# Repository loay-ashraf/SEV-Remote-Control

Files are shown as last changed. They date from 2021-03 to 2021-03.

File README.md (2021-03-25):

# SEV Remote Control
Smart Electric Vehicle remote control implemented using AVR 8-bit microcontroller and Android companion app as a part of EV car conversion graduation project for Mechatronics Engineering Bachelor - Fall 2018.

## Overview
This section gives an overview of the system.

### Concept

SEV remote control is done via means of bluetooth communication between AVR controller board and any bluetooth-enabled device (Android smartphone for example).

### System Layout
System is divided into two separate modules that communicate with each other to acheive the desired output, which are:

#### SEV Controller Board Module

Controller board controls a set of relays and DAC units each connected to a specific actuator in the car.

#### SEV Companion App Module

Companion app sends commands via bluetooth to control each actuator.

## Discussion
This section discusses desicions made regarding design and implementation.

### Microcontroller

We opted for ATmega32 for SEV controller board as it has USART module and enough pins to control relays and DACs.

### Communication Protocol

We used USART protocol in order to communicate with the HC-05 bluetooth module.

### Android IDE

We used free MIT App Inventor as we lacked experience in Android app development while App Inventor offered shallow learning curve and a ton of tutorials available.

## Screenshots

[Screenshots of the companion app](Software/Companion%20App/Screenshots)

## Built With
- Atmel Studio 7 - The official AVR IDE
- AVR-gcc V5.4 - C compiler
- GNU Make - auto-generated makefile
- MIT App Inventor - Android IDE
- CadSoft EAGLE - PCB design tool

## Authors
Loay Ashraf - <loay.ashraf.96@gmail.com>

Mohamed Gamal - <muhammed.gamal051@gmail.com>

## License
This project is licensed under the MIT License - see the LICENSE.md file for details

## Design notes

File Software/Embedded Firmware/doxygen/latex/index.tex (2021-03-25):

\begin{DoxyAuthor}{Author}
Loay Ashraf \href{mailto:loay.ashraf.96@gmail.com}{\tt loay.\+ashraf.\+96@gmail.\+com} 
\end{DoxyAuthor}
\begin{DoxyVersion}{Version}
1.\+0.\+0
\end{DoxyVersion}
This program is implemented on A\+Tmega16/32 running at 16 M\+HZ C\+PU clock, it basically receives commands from Android companion application via Bluetooth using the widely common H\+C-\/05 Bluetooth Module, it acts upon the command received by -\/for example-\/ turning ON a relay which activates certain feature of the vehicle; means of feedback include battery voltage and speed of the motor.

\begin{DoxySeeAlso}{See also}
\mbox{\hyperlink{main_8c}{main.\+c}} 
\end{DoxySeeAlso}

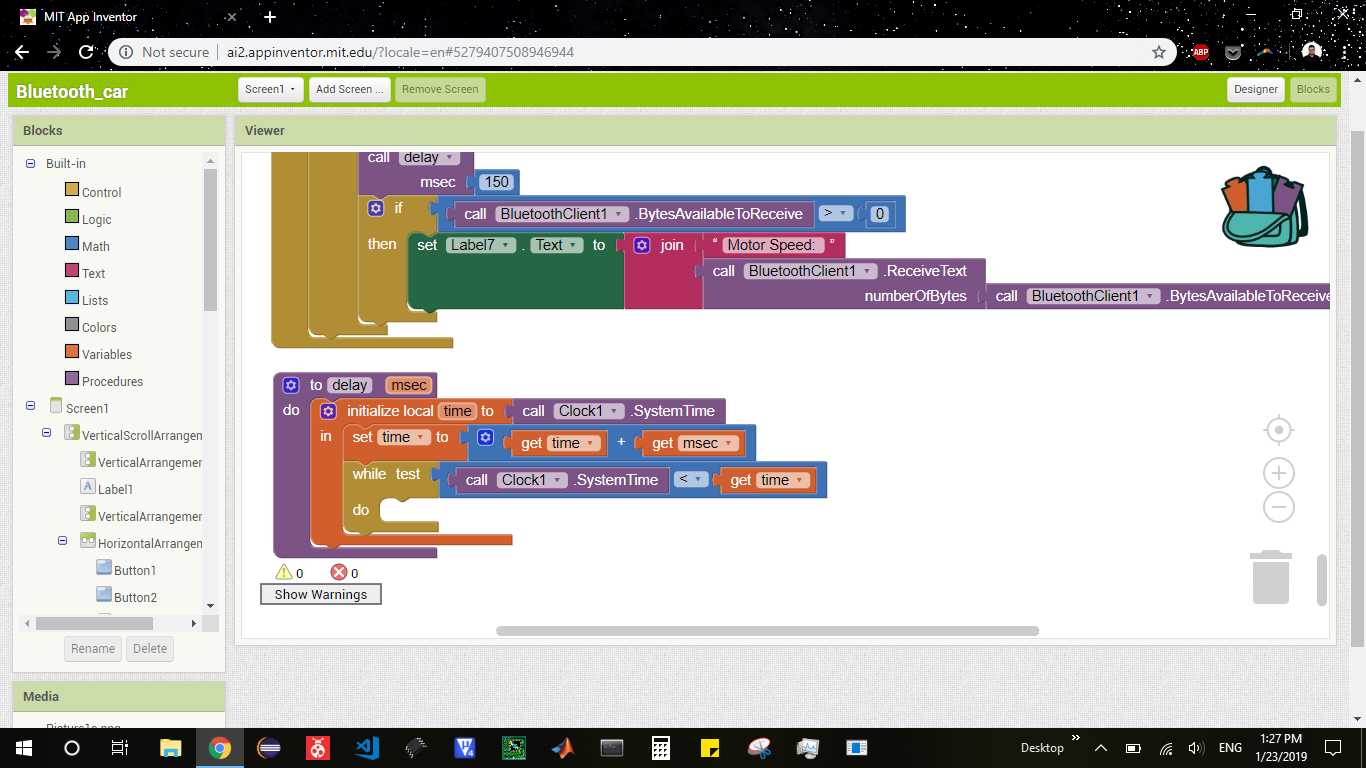
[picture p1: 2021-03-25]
Software/Companion App/Screenshots/App inventor/Screenshot (27).png

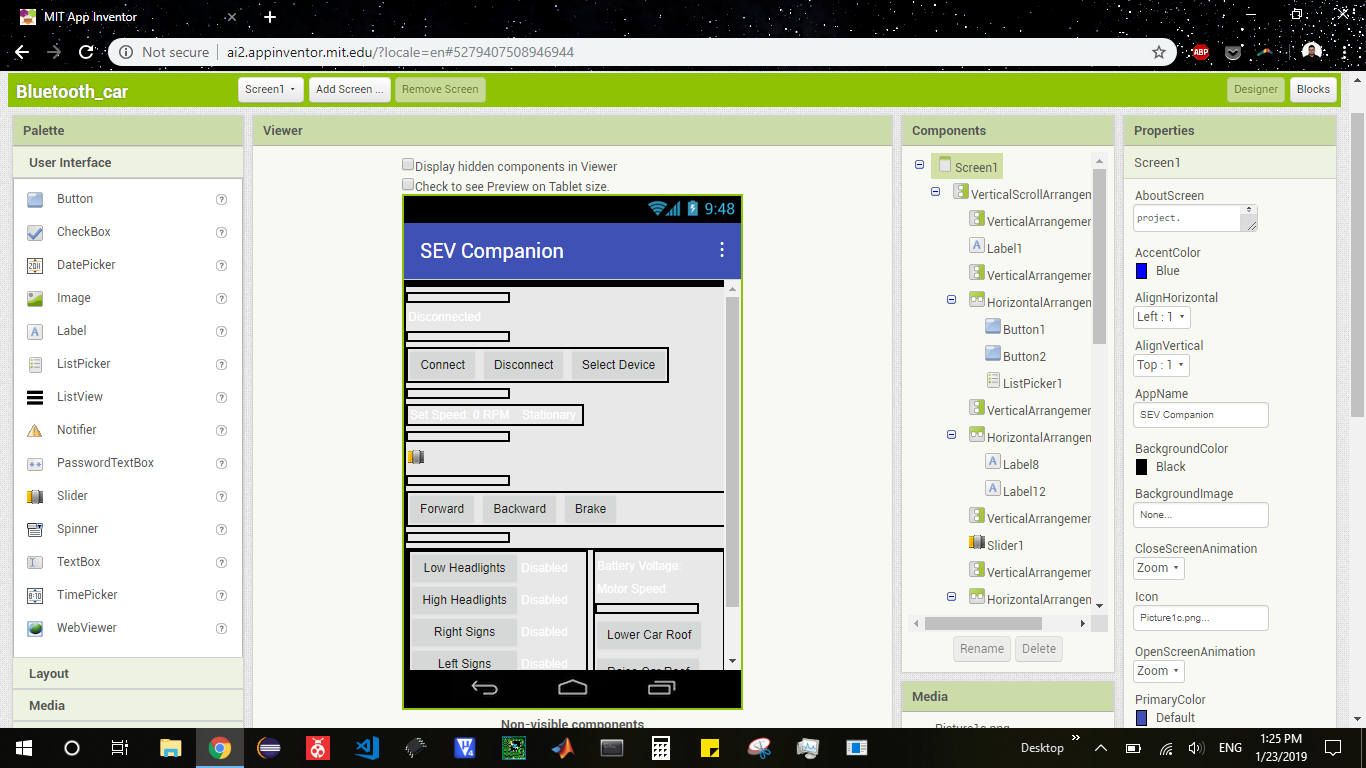
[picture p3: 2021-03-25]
Software/Companion App/Screenshots/App inventor/Screenshot (18).png

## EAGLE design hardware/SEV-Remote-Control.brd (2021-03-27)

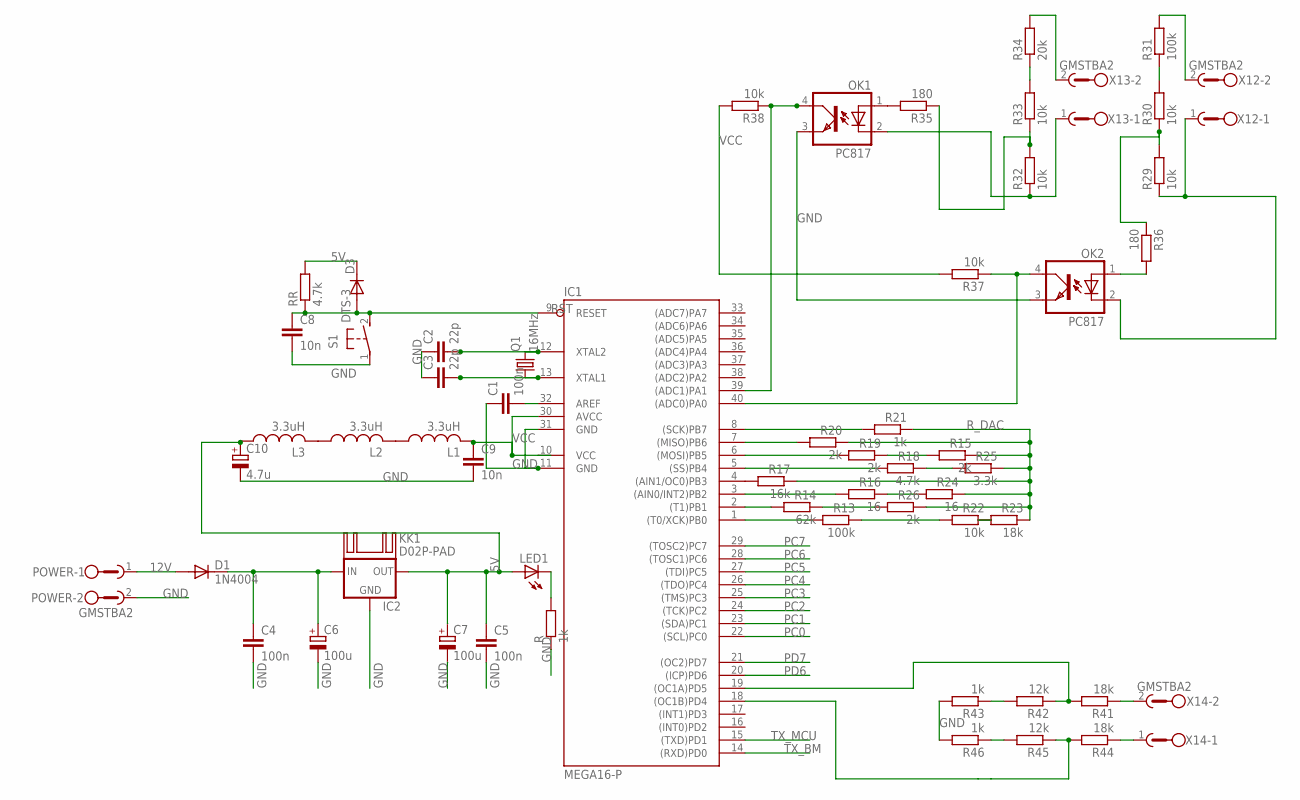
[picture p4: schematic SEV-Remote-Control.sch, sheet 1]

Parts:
C1, C4, C5: 100n; C025-025X050
C2, C3: 22p; C025-025X050
C6, C7: 100u; E2,5-6
C8, C9: 10n; C025-025X050
C10: 4.7u; E2,5-6
D1: 1N4004; DO41-10
D3: 1N4148DO35-10; DO35-10
IC1: MEGA16-P; DIL40
IC2: 78XXS
KK1: D02P-PAD; D02PA-PAD
L1, L2, L3: 3.3uH; 0207/7
LED1: LED5MM
OK1, OK2: PC817; DIL04
POWER: GMSTBA2
Q1: 16MHz; HC49/S
R, R21, R43, R46: 1k; 0207/10
R13, R31: 100k; 0207/10
R14: 62k; 0207/10
R15, R19, R20, R26: 2k; 0207/10
R16, R24: 16; 0207/10
R17: 16k; 0207/10
R18: 4.7k; 0207/10
R22, R29, R30, R32, R33, R37, R38: 10k; 0207/10
R23, R41, R44: 18k; 0207/10
R25: 3.3k; 0207/10
R34: 20k; 0207/10
R35, R36: 180; 0207/10
R42, R45: 12k; 0207/10
RR: 4.7k; 0207/10
S1: DTS-3
X12, X13, X14: GMSTBA2

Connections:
5V: C5.1, C7.+, C10.+, D3.C, IC2.OUT, L3.1, LED1.A, RR.2
12V: D1.A, POWER.1; also elsewhere on the board
GND: C1.1, C2.1, C3.1, C4.2, C5.2, C6.-, C7.-, C8.2, C9.2, C10.-, IC1.11 (GND), IC1.31 (GND), IC2.GND, OK1.3 (EMIT), OK2.3 (EMIT), POWER.2, R.1, R43.2, R46.2, S1.1; also elsewhere on the board
IN: C4.1, C6.+, D1.C, IC2.IN
unnamed: R15.2, R19.1
unnamed: R13.1, R22.2
unnamed: LED1.K (C), R.2
unnamed: C2.2, IC1.12 (XTAL2), Q1.2
unnamed: R22.1, R23.2
unnamed: C1.2, IC1.32 (AREF)
unnamed: R16.1, R24.2
unnamed: C3.2, IC1.13 (XTAL1), Q1.1
unnamed: R18.1, R25.2
unnamed: R14.1, R26.2
unnamed: L1.1, L2.2
unnamed: L2.1, L3.2
unnamed: R29.2, R30.1, R36.1
unnamed: R30.2, R31.1
unnamed: R31.2, X12.2
unnamed: IC1.40 ((ADC0)PA0), OK2.4 (COL), R37.1
unnamed: OK1.1 (A), R35.2
unnamed: R33.2, R34.1
unnamed: R34.2, X13.2
unnamed: OK1.2 (C), R32.1, X13.1
unnamed: R32.2, R33.1, R35.1
unnamed: OK2.1 (A), R36.2
unnamed: IC1.2 ((T1)PB1), R14.2
unnamed: OK2.2 (C), R29.1, X12.1
unnamed: IC1.39 ((ADC1)PA1), OK1.4 (COL), R38.1
unnamed: R44.1, X14.1
unnamed: IC1.1 ((T0/XCK)PB0), R13.2
unnamed: IC1.3 ((AIN0/INT2)PB2), R16.2
unnamed: IC1.4 ((AIN1/OC0)PB3), R17.2
unnamed: IC1.5 ((SS)PB4), R18.2
unnamed: IC1.6 ((MOSI)PB5), R19.2
unnamed: IC1.7 ((MISO)PB6), R20.2
unnamed: IC1.8 ((SCK)PB7), R21.2
unnamed: R41.1, X14.2
unnamed: IC1.19 ((OC1A)PD5), R41.2, R42.1
unnamed: IC1.18 ((OC1B)PD4), R44.2, R45.1
unnamed: R42.2, R43.1
unnamed: R45.2, R46.1
PC0: IC1.22 ((SCL)PC0); also elsewhere on the board
PC1: IC1.23 ((SDA)PC1); also elsewhere on the board
PC2: IC1.24 ((TCK)PC2); also elsewhere on the board
PC3: IC1.25 ((TMS)PC3); also elsewhere on the board
PC4: IC1.26 ((TDO)PC4); also elsewhere on the board
PC5: IC1.27 ((TDI)PC5); also elsewhere on the board
PC6: IC1.28 ((TOSC1)PC6); also elsewhere on the board
PC7: IC1.29 ((TOSC2)PC7); also elsewhere on the board
PD6: IC1.20 ((ICP)PD6); also elsewhere on the board
PD7: IC1.21 ((OC2)PD7); also elsewhere on the board
RST: C8.1, D3.A, IC1.9 (RESET), RR.1, S1.2
R_DAC: R15.1, R17.1, R20.1, R21.1, R23.1, R24.1, R25.1, R26.1; also elsewhere on the board
TX_BM: IC1.14 ((RXD)PD0); also elsewhere on the board
TX_MCU: IC1.15 ((TXD)PD1); also elsewhere on the board
VCC: C9.1, IC1.10 (VCC), IC1.30 (AVCC), L1.2, R37.2, R38.2; also elsewhere on the board

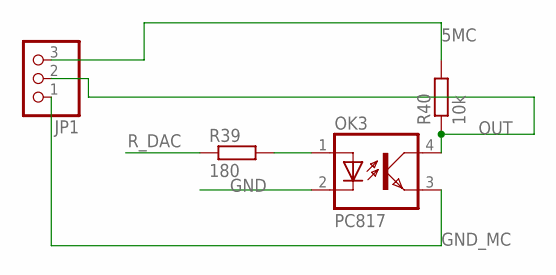
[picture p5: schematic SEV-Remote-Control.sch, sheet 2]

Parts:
JP1: PINHD-1X3; 1X03
OK3: PC817; DIL04
R39: 180; 0207/10
R40: 10k; 0207/10

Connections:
5MC: JP1.3, R40.2
GND: OK3.2 (C); also elsewhere on the board
GND_MC: JP1.1, OK3.3 (EMIT)
unnamed: OK3.1 (A), R39.2
OUT: JP1.2, OK3.4 (COL), R40.1
R_DAC: R39.1; also elsewhere on the board

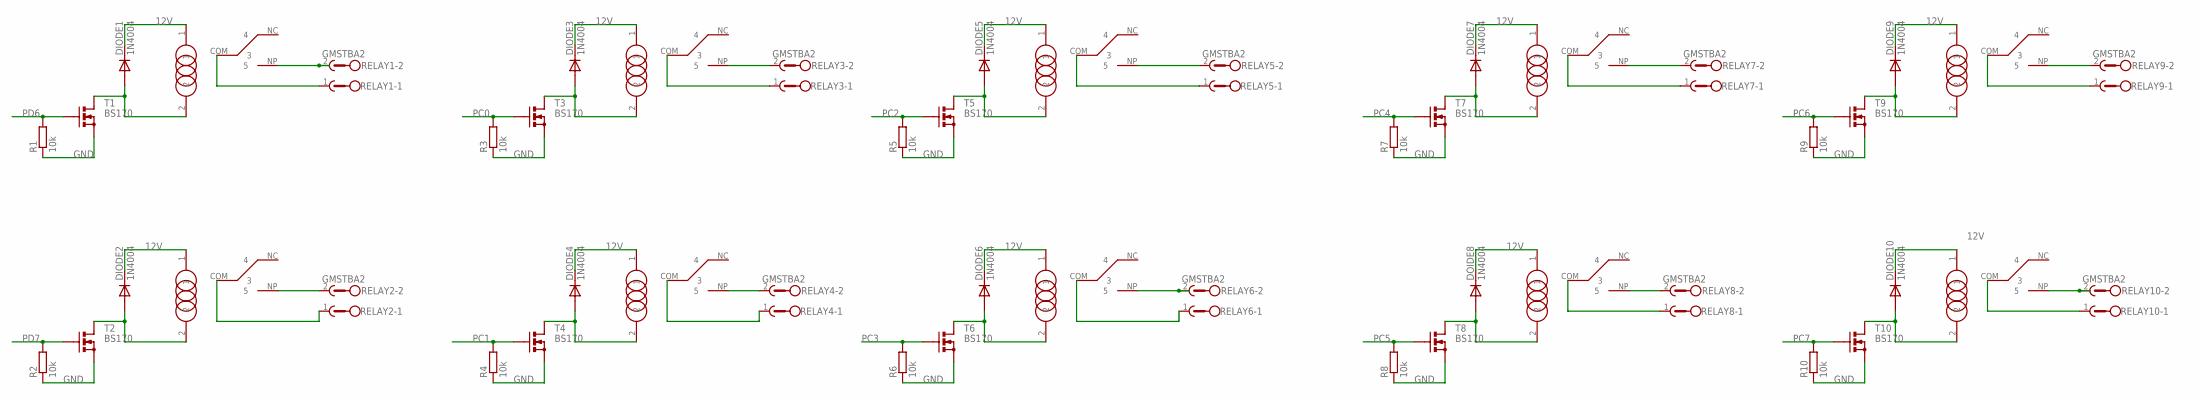
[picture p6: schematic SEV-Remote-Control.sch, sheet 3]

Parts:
DIODE1, DIODE2, DIODE3, DIODE4, DIODE5, DIODE6, DIODE7, DIODE9, DIODE10: 1N4004; DO41-10
DOIDE8: 1N4004; DO41-10
R1, R2, R3, R4, R5, R6, R7, R8, R9, R10: 10k; 0207/10
REL3: RELAY
RELAY1, RELAY2, RELAY3, RELAY4, RELAY5, RELAY6, RELAY7, RELAY8, RELAY9, RELAY10: GMSTBA2
T1, T2, T3, T4, T5, T6, T7, T8, T9, T10: BS170; SOT54E
U$1, U$2, U$3, U$5, U$6, U$7, U$8, U$9, U$10: RELAY

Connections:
12V: DIODE1.C, DIODE2.C, DIODE3.C, DIODE4.C, DIODE5.C, DIODE6.C, DIODE7.C, DIODE9.C, DIODE10.C, DOIDE8.C, REL3.1, U$1.1, U$2.1, U$3.1, U$5.1, U$6.1, U$7.1, U$8.1, U$9.1, U$10.1; also elsewhere on the board
COM: RELAY10.1, U$3.COM (3)
COM1: RELAY2.1, U$9.COM (3)
GND: R1.1, R2.1, R3.1, R4.1, R5.1, R6.1, R7.1, R8.1, R9.1, R10.1, T1.S, T2.S, T3.S, T4.S, T5.S, T6.S, T7.S, T8.S, T9.S, T10.S; also elsewhere on the board
unnamed: REL3.COM (3), RELAY3.1
unnamed: DIODE3.A, REL3.2, T3.D
unnamed: RELAY8.1, U$1.COM (3)
unnamed: DOIDE8.A, T8.D, U$1.2
unnamed: DIODE9.A, T9.D, U$2.2
unnamed: RELAY9.2, U$2.NP (5)
unnamed: RELAY6.2, U$8.NP (5)
unnamed: DIODE10.A, T10.D, U$3.2
unnamed: DIODE6.A, T6.D, U$8.2
unnamed: DIODE2.A, T2.D, U$9.2
unnamed: RELAY7.2, U$10.NP (5)
unnamed: REL3.NP (5), RELAY3.2
unnamed: DIODE7.A, T7.D, U$10.2
unnamed: RELAY4.1, U$5.COM (3)
unnamed: DIODE4.A, T4.D, U$5.2
unnamed: RELAY9.1, U$2.COM (3)
unnamed: RELAY5.1, U$6.COM (3)
unnamed: RELAY8.2, U$1.NP (5)
unnamed: RELAY4.2, U$5.NP (5)
unnamed: RELAY6.1, U$8.COM (3)
unnamed: RELAY1.1, U$7.COM (3)
unnamed: RELAY7.1, U$10.COM (3)
unnamed: DIODE5.A, T5.D, U$6.2
unnamed: RELAY5.2, U$6.NP (5)
unnamed: DIODE1.A, T1.D, U$7.2
unnamed: RELAY1.2, U$7.NP (5)
NP1: RELAY2.2, U$9.NP (5)
PC0: R3.2, T3.G; also elsewhere on the board
PC1: R4.2, T4.G; also elsewhere on the board
PC2: R5.2, T5.G; also elsewhere on the board
PC3: R6.2, T6.G; also elsewhere on the board
PC4: R7.2, T7.G; also elsewhere on the board
PC5: R8.2, T8.G; also elsewhere on the board
PC6: R9.2, T9.G; also elsewhere on the board
PC7: R10.2, T10.G; also elsewhere on the board
PD6: R1.2, T1.G; also elsewhere on the board
PD7: R2.2, T2.G; also elsewhere on the board
RELAY6: RELAY10.2, U$3.NP (5)

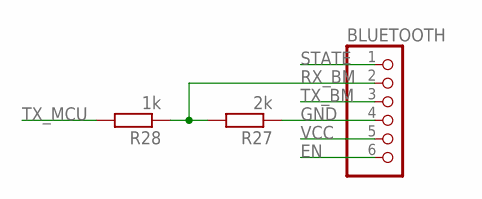
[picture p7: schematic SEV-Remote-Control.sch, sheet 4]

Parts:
BLUETOOTH: PINHD-1X6; 1X06
R27: 2k; 0207/10
R28: 1k; 0207/10

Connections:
EN: BLUETOOTH.6
GND: BLUETOOTH.4, R27.1; also elsewhere on the board
RX_BM: BLUETOOTH.2, R27.2, R28.1
STATE: BLUETOOTH.1
TX_BM: BLUETOOTH.3; also elsewhere on the board
TX_MCU: R28.2; also elsewhere on the board
VCC: BLUETOOTH.5; also elsewhere on the board

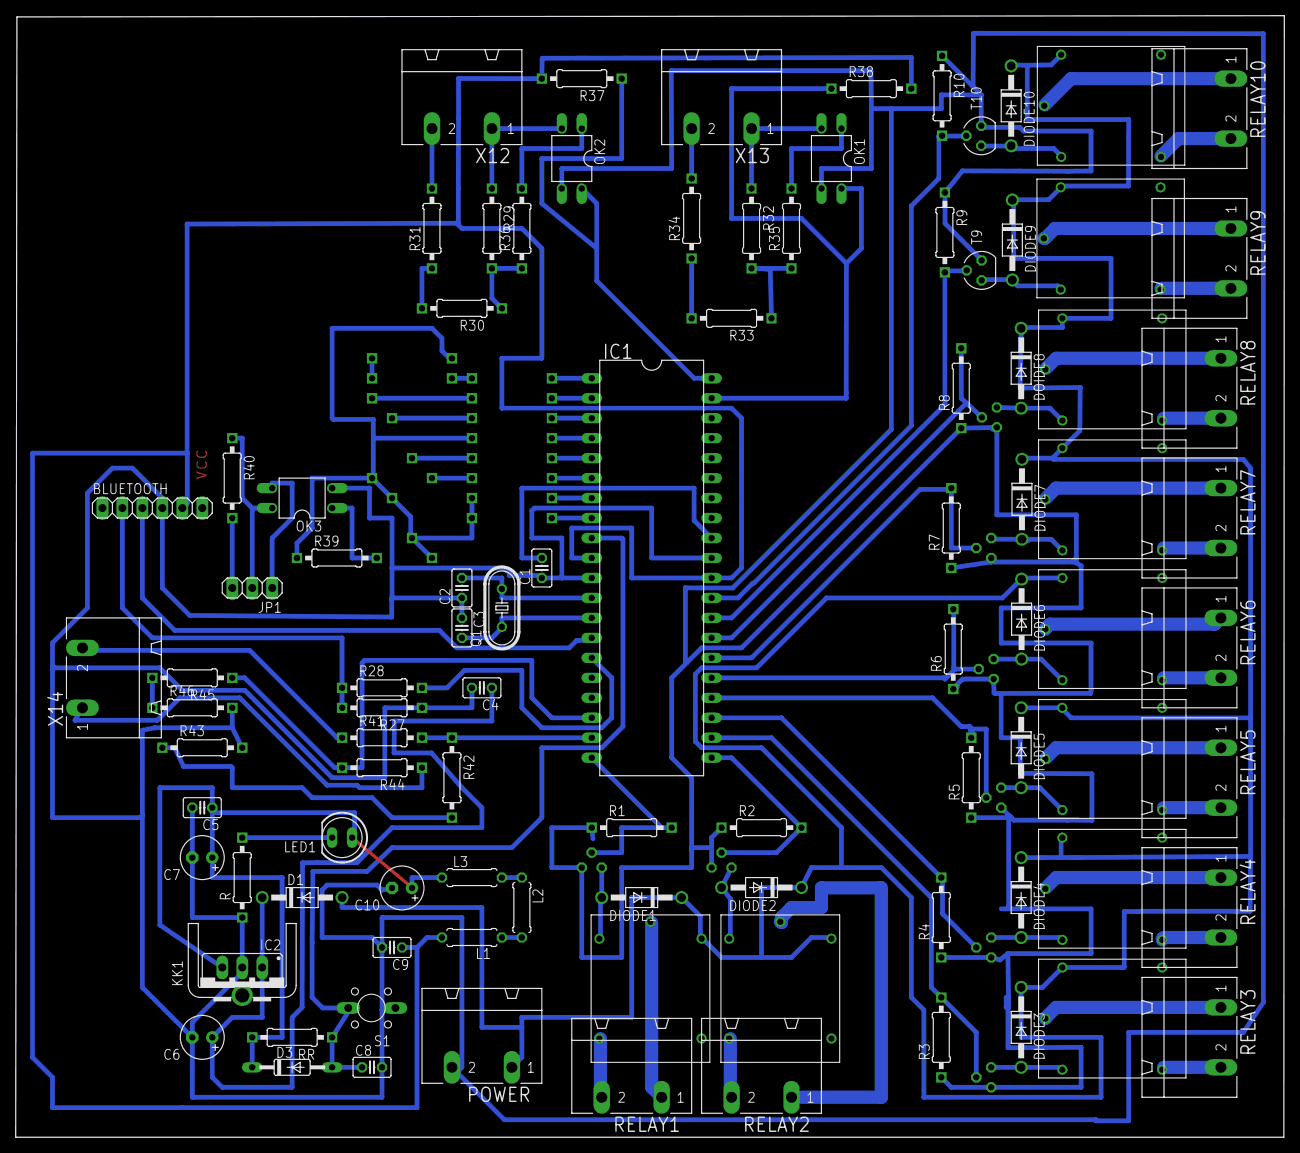
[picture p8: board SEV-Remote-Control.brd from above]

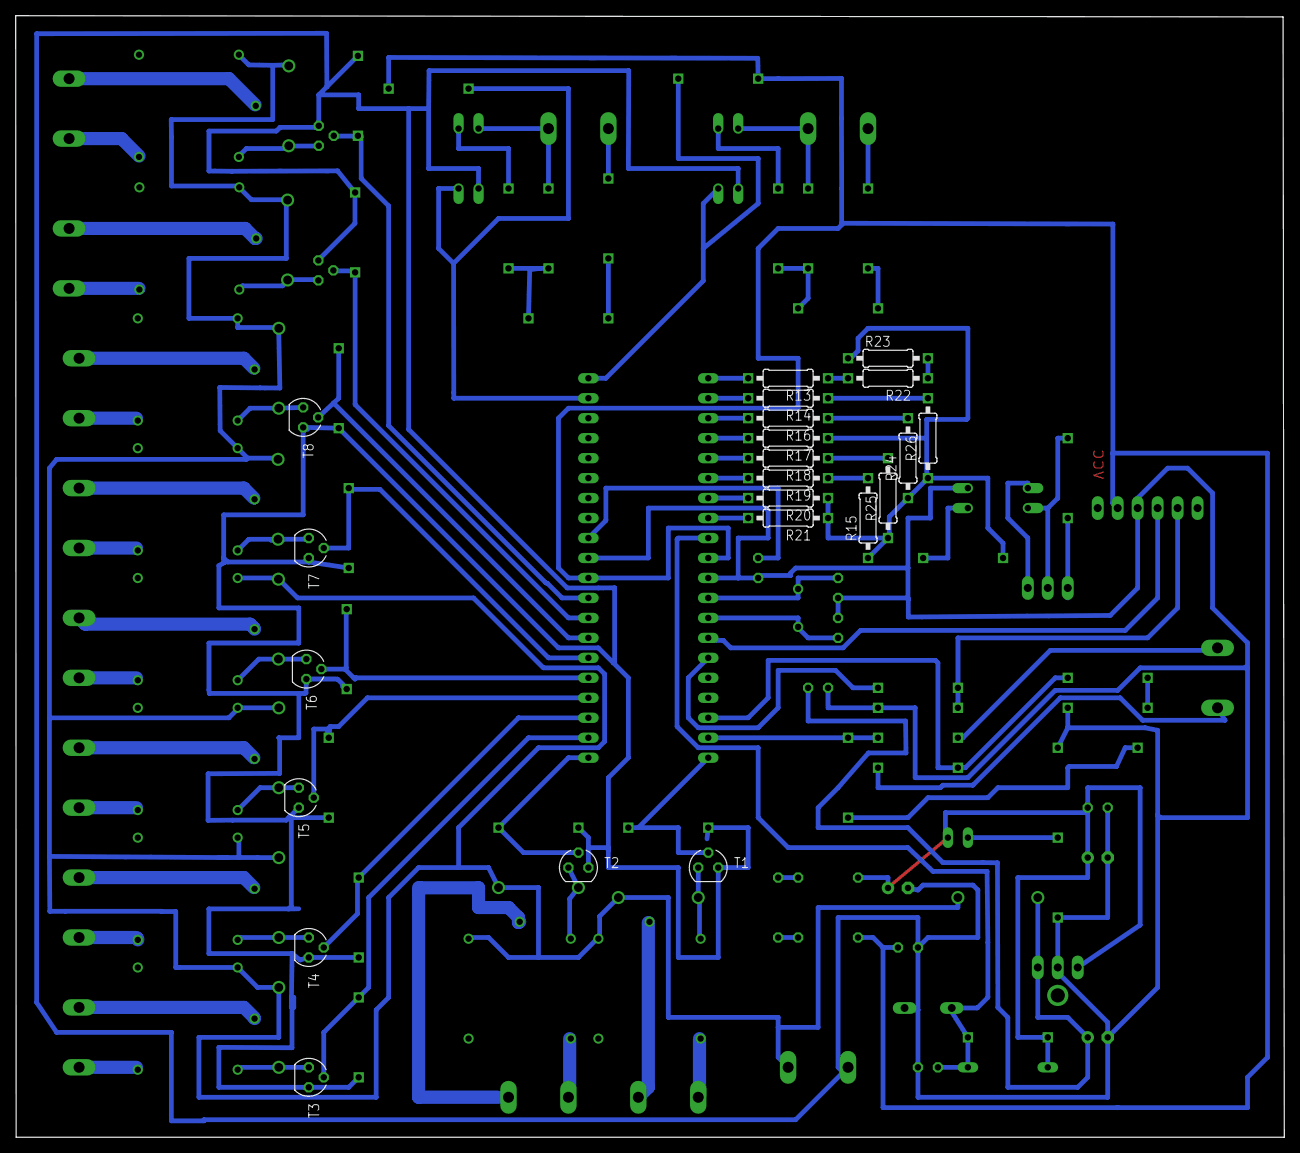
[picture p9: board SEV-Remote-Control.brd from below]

Board: 2 copper layers, 161.3 x 142.6 mm, 116 parts (22 on the bottom side), 92 nets.

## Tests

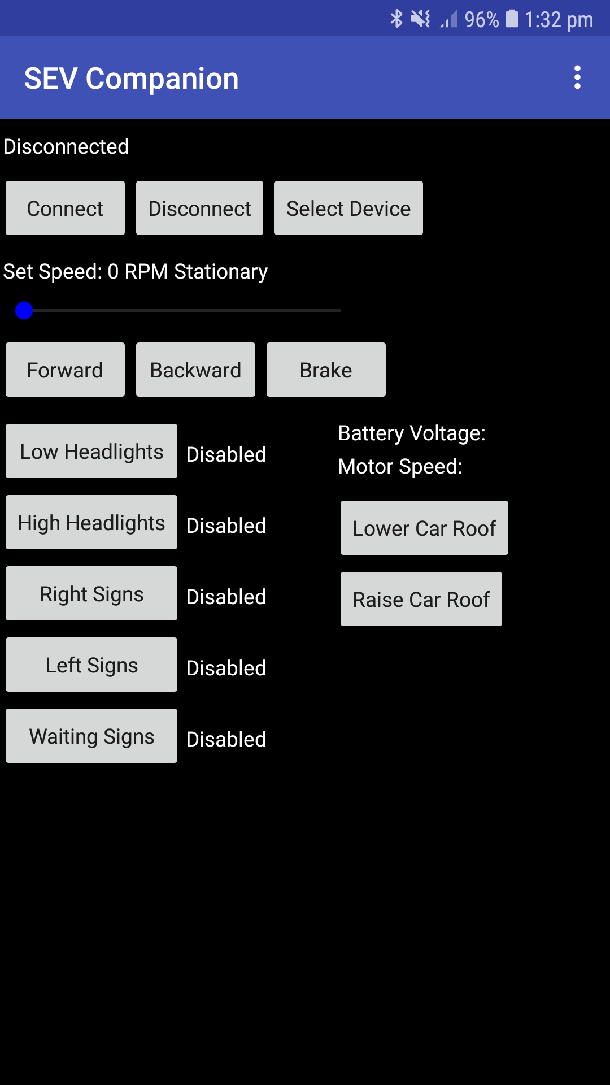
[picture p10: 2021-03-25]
Software/Companion App/Screenshots/Result APK/Screenshot_20190123-133213.jpg

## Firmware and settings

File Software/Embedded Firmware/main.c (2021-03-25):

/** @mainpage About
 *  @author Loay Ashraf <loay.ashraf.96@gmail.com>
 *  @version 1.0.0
 *
 *  This program is implemented on ATmega16/32 running at 16 MHZ
 *	CPU clock, it basically receives commands from Android companion
 *	application via Bluetooth using the widely common HC-05 Bluetooth 
 *	Module, it acts upon the command received by -for example- turning 
 *	ON a relay which activates certain feature of the vehicle; means of
 *	feedback include battery voltage and speed of the motor. 
 *  
 *	@pinassignments
 *
 *	- PB0-7: DAC output signal
 *	- PC0-7, PD6-7: Relay output signal
 *	- PD0: USART RX signal
 *	- PD1: USART TX signal
 *
 *	@see main.c
 */

/** @file main.c
 *  @brief includes the main function
 *  
 *	the main function periodically checks for incoming commands
 *	via USART interface, if one is received it starts processing 
 *	the command and takes the action that corresponds to the 
 *	command received. 
 *
 *  @author Loay Ashraf
 *	@version 1.0.0
 *  @pre include USART.h, string.h and set F_CPU in micro_config.h
 *  @bug no known bugs
 *  @see micro_config.h
 */

//------------INCLUDE DEVICE DRIVERS------------//

#include "ADC.h"
#include "USART.h"

//------------DECLARE GLOBAL VARIABLES------------//
/** @var char* received_ptr
 *  @brief Stores memory address of received command
 */

/** @var char* received_str
 *  @brief Stores data of received command
 */

/** @var char* res_str
 *  @brief Stores result of float conversion
 */

/** @var char* ON_flag
 *  @brief Stores ON status of the all features (0 for OFF, 1 for ON)
 */

/** @var float Volt
 *  @brief Current battery voltage value
 */

/** @var float Speed
 *  @brief Current motor speed value
 */

/** @var uint8 i
 *  @brief Counter that iterates through received command
 */

/** @var uint8 thumb_position
 *  @brief Stores current slider position in the android app
 */

char * received_ptr;
char received_str[10], res_str[7], ON_flag[7];
float Volt, Speed; 
uint8 i, thumb_position;

/** @brief the main function
 *
 *  see main.c description
 *
 *  @return exit status (1 or 0)
 */
int main(void){
	
	//------------INITIALIZE I/O PORTS------------//
	
	DDRB = 0xFF;
	DDRC = 0xFF;
	DDRD = 0xC0;
	
	//------------INITIALIZE ADC INTERFACE------------//
	
	ADC_Init(AVCC, RIGHT_ADJ, 128);	// AVCC as Vref, right adjusted result (10-bit), 128 prescaler
	ADC_Read(ADC0);
	ADC_Read(ADC1);
	
	//------------INITIALIZE USART INTERFACE------------//
	
	USART_init(AS, NORMAL_SPEED, 8, NO_PARITY, 1);	// asynchronous, 8-bit data frame, no parity check, one stop bit
	USART_set_baudrate(38400);						// 38400 bits/sec baud rate
	USART_enable();									// enable USART interface

	while (1){
		
		//------------RECIEVE NEW COMMAND AND PROCESS IT INTO A STRING------------//
		
		received_ptr = USART_Receive_str();		// receive new command
		for(i=0;i<10;i++)
		received_str[i]=*received_ptr++;		// store received command data in array
		
		//------------CHECK RECEIVED COMMAND AND TAKE CORRESPONDING ACTION------------//
		
		if(!strcmp(received_str,"Voltage")){
			
			Volt = ((ADC_Read(ADC0)/1023.0)*60);
			dtostrf(Volt, 6, 2,res_str);
			USART_Transmit_str(res_str);

		}else if (!strcmp(received_str,"RPM")){
			
			Speed = ((ADC_Read(ADC1)/1023.0)*4900);
			dtostrf(Speed, 6, 2,res_str);
			USART_Transmit_str(res_str);
			
		}else if (!strcmp(received_str,"one")){
			
			// forward action
			PORTC |= 0x01;

		}else if (!strcmp(received_str,"two")){
			
			// reverse action
			PORTC |= 0x02;
			_delay_ms(1);
			PORTC |= 0x01;
	
		}else if (!strcmp(received_str,"three")){
			
			// brake action
			PORTC |= 0x04;
			_delay_ms(1);
			PORTC &= ~0x03;
			_delay_ms(10);
			PORTC &= ~0x04;

		}else if (!strcmp(received_str,"four")){
			
			// low headlights
			if(!ON_flag[0]){
			PORTC |= 0x08;
			ON_flag[0] = 1;
			}else{
			PORTC &= ~0x08;	
			ON_flag[0] = 0;	
			}

		}else if (!strcmp(received_str,"five")){
			
			// high headlights
			if(!ON_flag[1]){
			PORTC |= 0x10;
			ON_flag[1] = 1;
			}else{
			PORTC &= ~0x10;
			ON_flag[1] = 0;
			}

		}else if (!strcmp(received_str,"six")){
			
			// right signs
			if(!ON_flag[2]){
			PORTC |= 0x20;
			ON_flag[2] = 1;
			}else{
			PORTC &= ~0x20;
			ON_flag[2] = 0;
			}

		}else if (!strcmp(received_str,"seven")){
			
			// left signs
			if(!ON_flag[3]){
			PORTC |= 0x40;
			ON_flag[3] = 1;
			}else{
			PORTC &= ~0x40;
			ON_flag[3] = 0;
			}

		}else if (!strcmp(received_str,"eight")){
			
			// waiting signs
			if(!ON_flag[4]){
			PORTC |= 0x80;
			ON_flag[4] = 1;
			}else{
			PORTC &= ~0x80;
			ON_flag[4] = 0;
			}

		}else if (!strcmp(received_str,"nine")){
			
			// lower car roof
			if(!ON_flag[5]){
			PORTD |= 0x40;
			ON_flag[5] = 1;
			}else{
			PORTD &= ~0x40;
			ON_flag[5] = 0;
			}

		}else if (!strcmp(received_str,"ten")){
			
			// raise car roof
			if(!ON_flag[6]){
			PORTD |= 0x80;
			ON_flag[6] = 1;
			}else{
			PORTD &= ~0x80;
			ON_flag[6] = 0;
			}

		}else{
			
			// receive slider position in the app and set speed
			thumb_position = atoi(received_str);
			PORTB = (255-thumb_position);
			
		}}
	}
